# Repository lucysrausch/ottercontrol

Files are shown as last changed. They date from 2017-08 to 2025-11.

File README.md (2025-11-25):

# OtterControl
Hardware files for OtterControl BLDC motor controller.

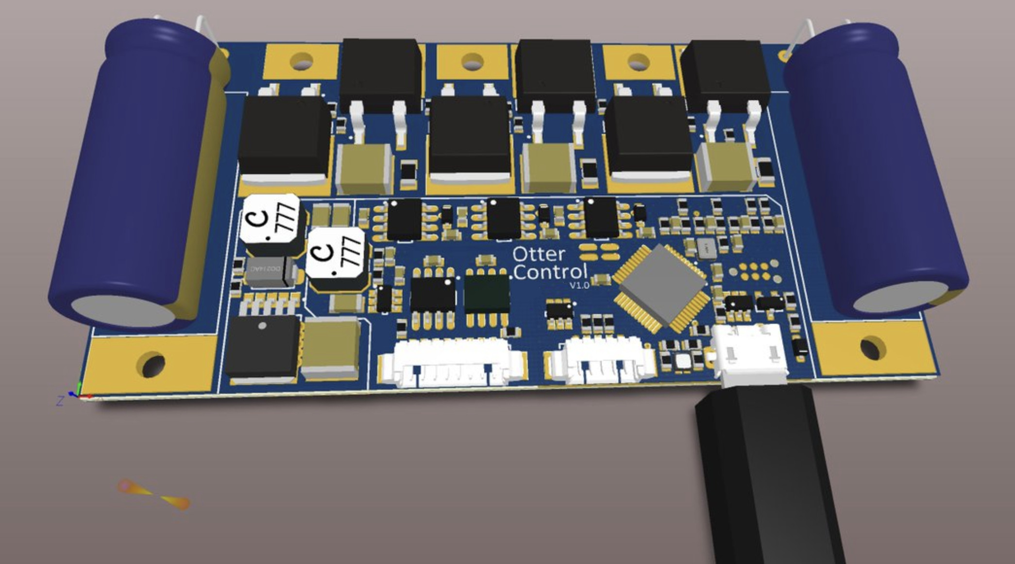
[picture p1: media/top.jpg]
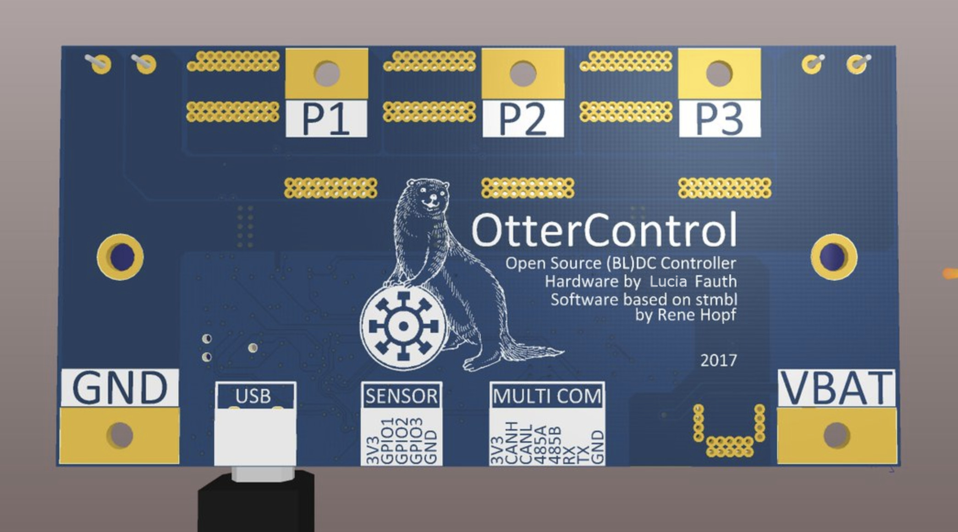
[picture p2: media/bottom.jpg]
   

## What is OtterControl?
OtterControl is a open source, open hardware DC / BLDC motor controller.
The basic idea was to make the well-known VESC (http://vedder.se/2015/01/vesc-open-source-esc/) even cheaper - making hoverboard-powered armchairs or crazycarts affordable.

While these 350W hoverboards motors are great and quiet affordable (only 40€ in Germany),
you need a powerful ESC to get them running. Until now, the only open ESC I'm aware of is the VESC - which is great and all, but with ~100-120€ per piece quiet expensive.
That's why I decided to save on some parts:

* Single-Chip Gatedrivers
* Mosfets in D2PAK package
* Chinese HV buck converter
* STM32f3 instead of f4: still powerful enough, and with more internal analog peripherals

The STM32f303 has lots of internal peripherals such as OpAmps, PGAs etc.
Using this chip reduces external components and system complexity - saving about 10€.
Also, using D2PAK Mosfets allows more flexible part selection - saving another 20€ with almost the same specs.

The final BOM for 50pcs of OtterControl turns out to be ~19€ per piece.

## Specs
* max. 50A continous motor current (~90A peak)
* max. 80V (with 63V capacitors = 14S LiIon)
* STMBL Codebase ("easy to use", configurable)
* no additional programming device (USB DFU support)

* UART, RS485, CAN, USB
* PPM (to be implemented)

* 3 GPIOs, sharing one Timer (eg. as hall sensor input, quadrature encoder)
* 5V max. 200mA out (eg. for hall sensors)
* Otter

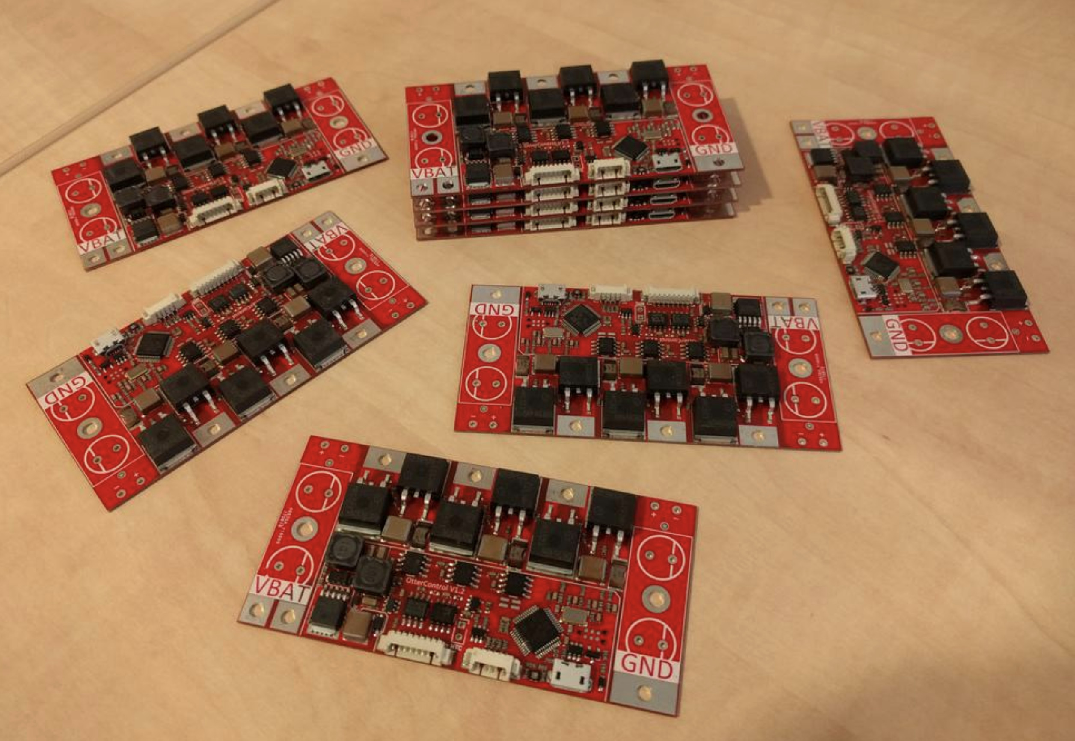
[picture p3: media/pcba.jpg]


## Versions

There are currently two different versions of OtterControl V1.3:
One with 1mOhm current-sensing shunts, and one with 3mOhm.
The reason for this:

To measure the phase current, the f303 internal PGA is set to 16x gain.
This gives a input range of 3.2AVDD / 16 = 200mV.
It is necessary to measure positiv and negative currents, so the shunt is pre-biased to 100mV, giving +/- 100mV measurable voltage drop.

* With 1mOhm, this means 100A full scale
* With 3mOhm, this means 33A full scale

Depending on your application, you want as much current resolution as possible.
For a 5A DC motor, or a small BLDC, 33A is way enough, archiving good current regulation.
However, for applications with more current, 1mOhm increases the current scale to the necessary range.

## Software

OtterControl is based on the stmbl codebase (https://github.com/rene-dev/stmbl).
A ported version can be found in my fork (ottercontrol branch).
Essentially, the code on the f303 is the same as in stmbl, but without the f4 this mcu now also handles encoder input, position regulation, user settings etc.

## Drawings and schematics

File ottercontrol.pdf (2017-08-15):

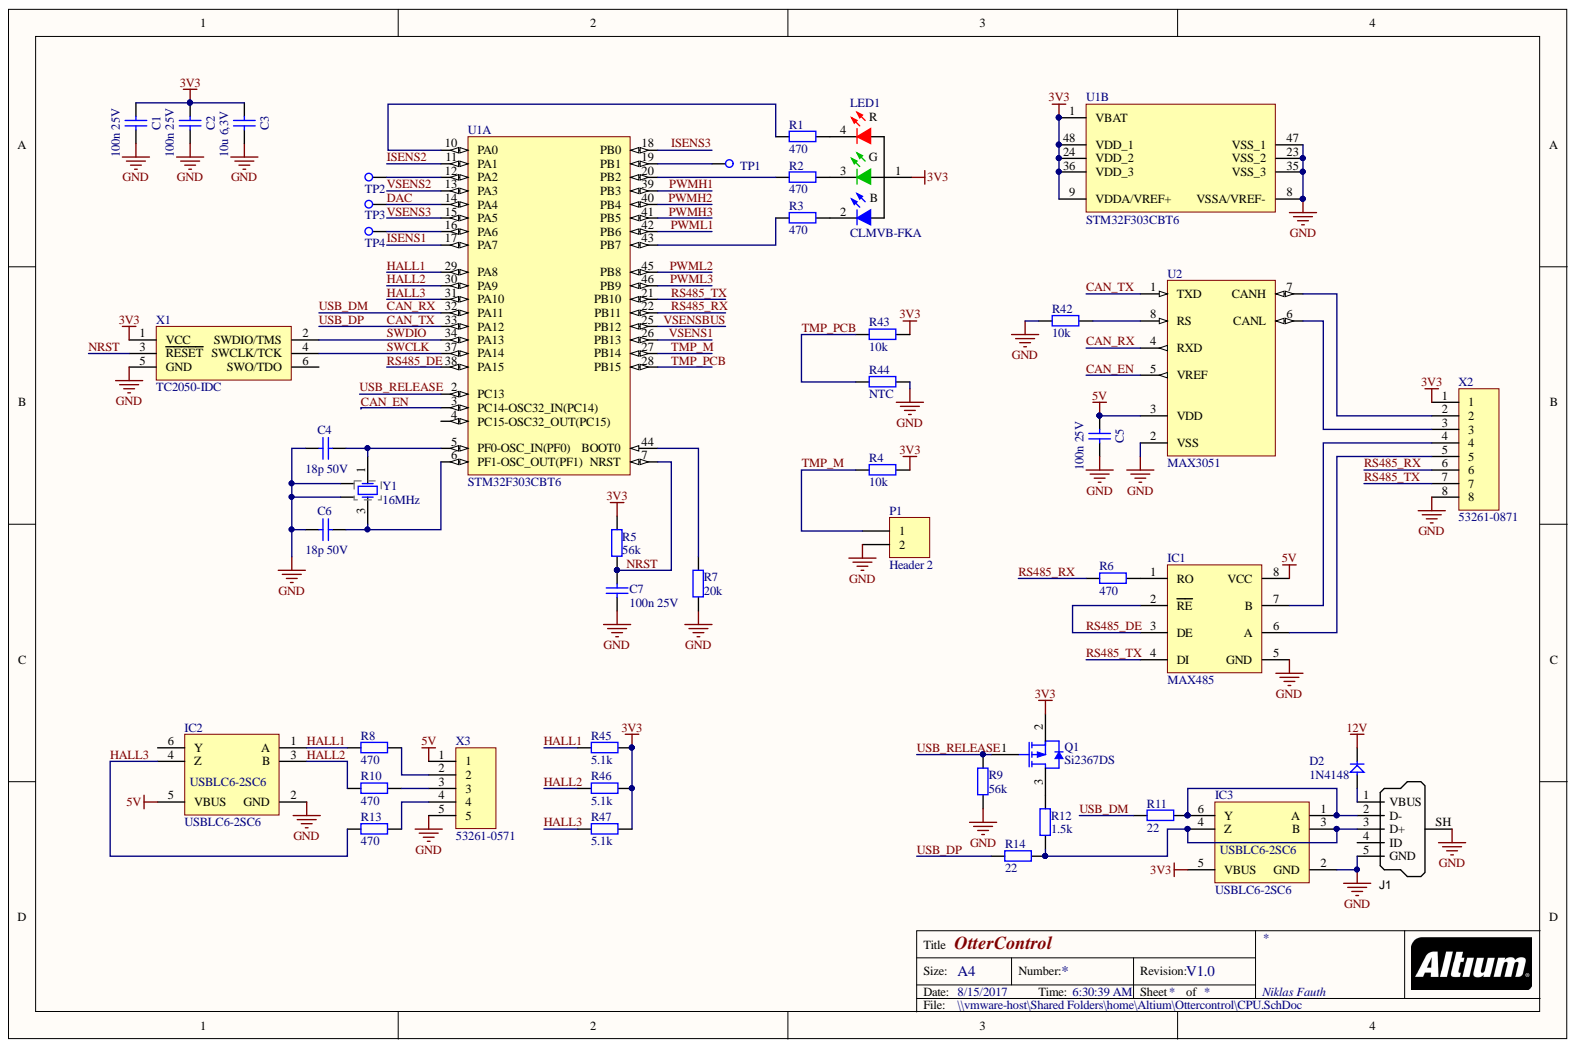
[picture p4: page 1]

VSS 2 | | 3 3

OtterControl Title | * Niklas Fauth

Size: A4 | Number: * | Revision: V1.0

Date: 8/15/2017 Time: 6:30:39 AM | | Sheet * of *
File: \\vmware-host\Shared Folders\home\Altium\Ottercontrol\CPU.SchDoc

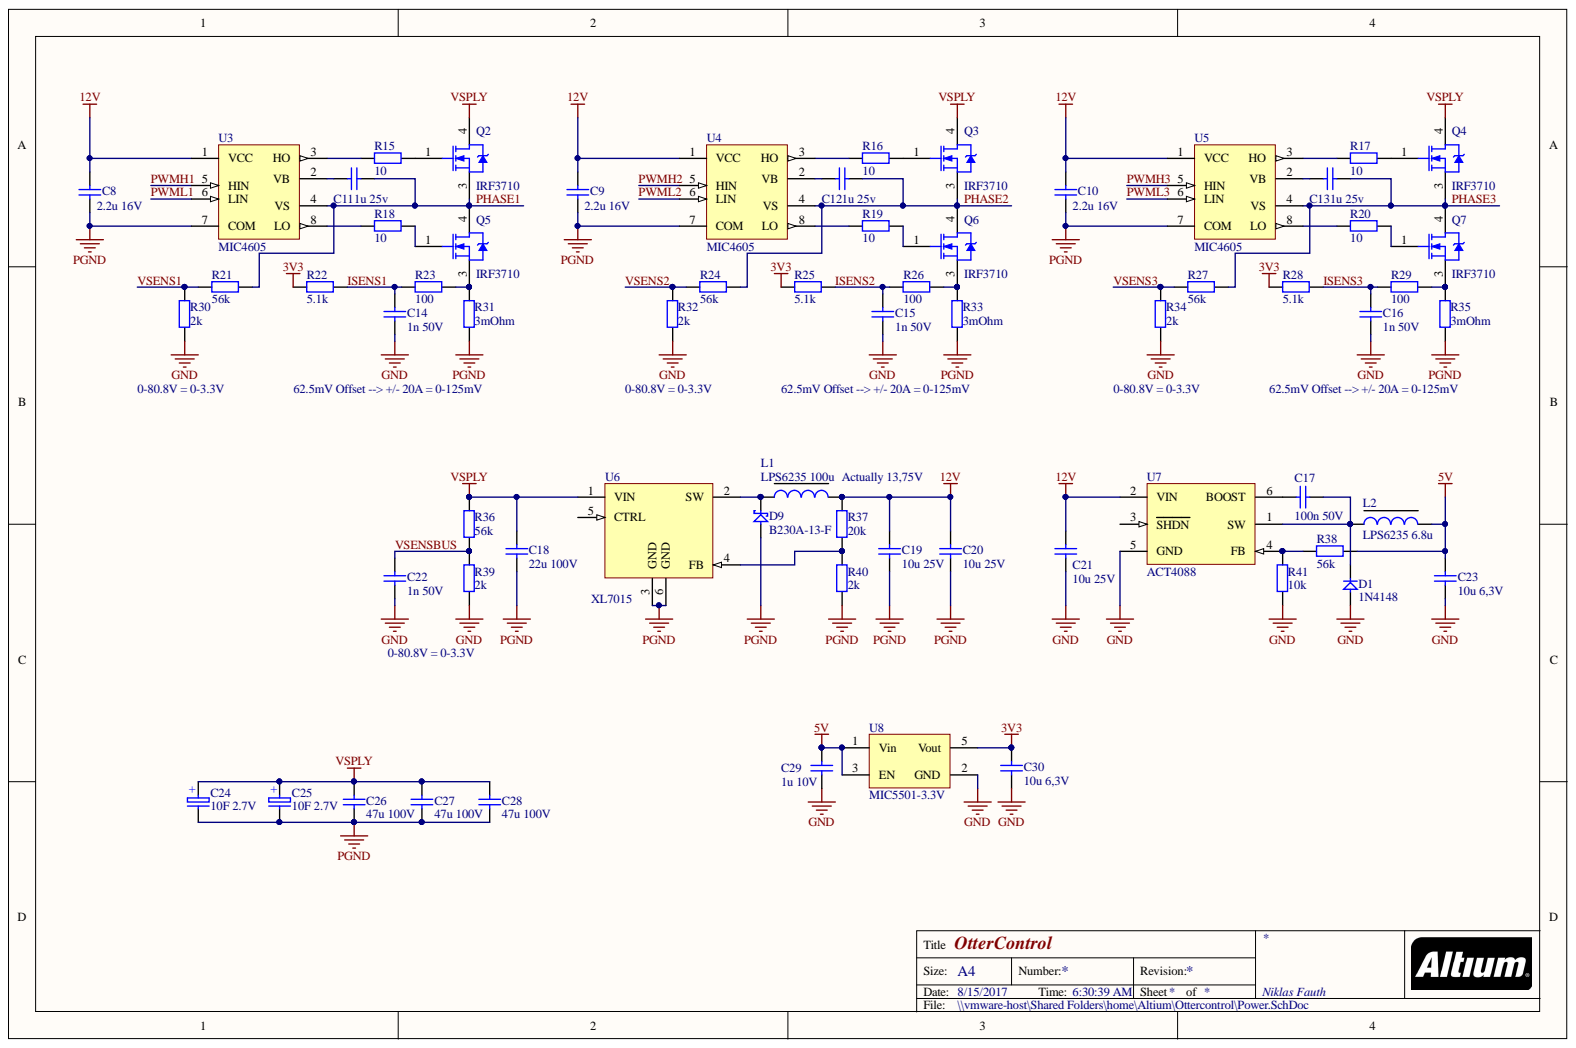
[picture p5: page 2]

HIN 5 LIN 6 | HIN 5 LIN 6 | HIN 5 LIN 6

OtterControl Title | * Niklas Fauth

Size: A4 | Number: * | Revision: *

Date: 8/15/2017 Time: 6:30:39 AM | | Sheet * of *
File: \\vmware-host\Shared Folders\home\Altium\Ottercontrol\Power.SchDoc

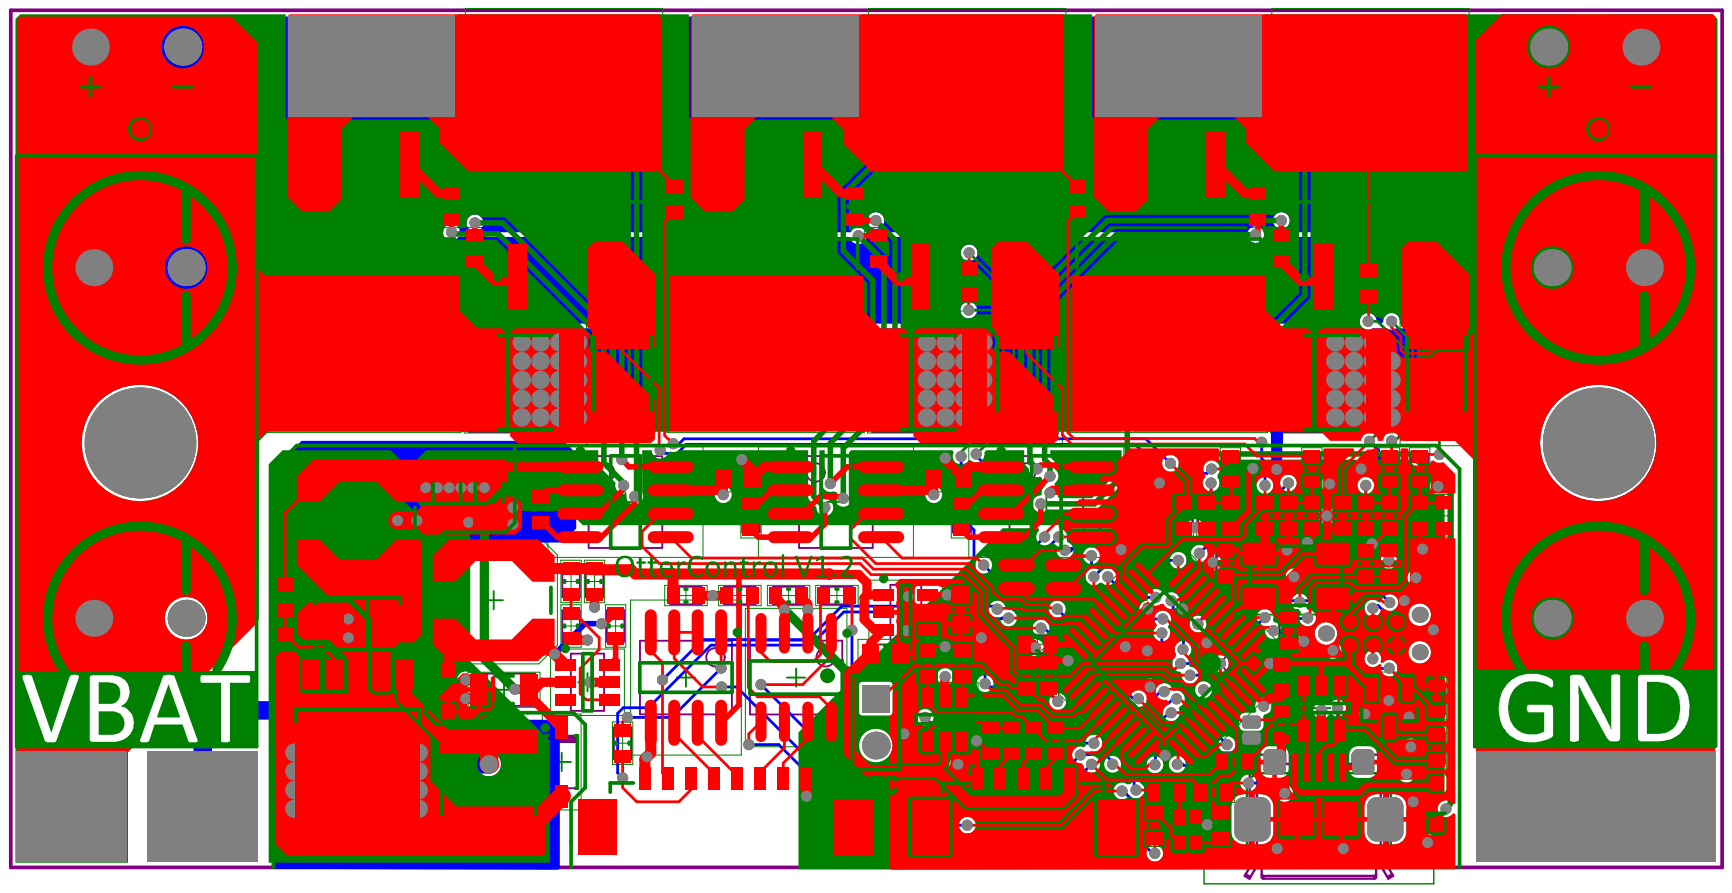
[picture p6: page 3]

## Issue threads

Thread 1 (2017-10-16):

Anfrage

Be-Sommer, 2017-10-16:
Hallo Niklas,
am Mittwoch war ich zu Besuch in der warpzone.
Für ein Jufo-Projekt, möchten wir zwei Motoren aus ´nem Hoverboard verwenden. Frederik (Kontakt über Jugend forscht) hat sehr begeistert von den OtterControl-Boards geschwärmt. Kannst du uns zwei der Boards verkaufen? Frederik sagte auch, dass du die Anschlusskabel für die Hoverboardmotoren bereits konfektioniert hast, das macht die Sache auf jeden Fall robuster.
Kontakt: sommer(at)bkr-projekt.de

Grüße Berthold

P.S.: Mein Background - Ich bin Lehrer am Berufskolleg Rheine mit den Fächern Physik und Elektrotechnik. Des Weiteren begleite ich (recht intensiv) Schülerprojekte, meist im Bereich Technik. Vieles läuft bei Jugend forscht aber auch bei verschiedenen Maker Faires sind wir regelmäßig mit Schülerprojekten dabei. Bin ich viel zum Thema Maker Space und Schule unterwegs. (Maker Space trotz Schule - schlau werden ohne Langeweile.)

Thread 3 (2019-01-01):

HALL2 is shorted to HALL3

cyber-murmel, 2019-01-01:
According to the [USBLC6-2 data sheet](https://www.mouser.de/datasheet/2/389/usblc6-2-957370.pdf) pin 3 and pin 4 (as well as pin 1 and pin 6) are connected internally.

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

NiklasFauth, 2019-01-01:
sry should be USBLC6-4

cyber-murmel, 2019-01-01:
:+1:

Closed 2019-01-01.

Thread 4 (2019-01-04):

GND und PGND

cyber-murmel, 2019-01-04:
Wo in der schematic ist GND mit PGND verbunden? Ist es das ueberhaupt?

NiklasFauth, 2019-01-04:
There is a net tie between power and logic near the STM32. It is placed at this position so that the gnd return of the current shunts is roughly matched.

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

cyber-murmel, 2019-01-04:
Okay, but is the connection actually indicated in the schematic?

Closed 2019-01-04.

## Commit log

2017-08-13 ADD: design files for ottercontrol V1.2
    [CPU.SchDoc, Power.SchDoc]
2017-08-15 UPD: final V1.2 design files
    [CPU.SchDoc, Power.SchDoc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]
2025-11-25 ADD: pcb pics
